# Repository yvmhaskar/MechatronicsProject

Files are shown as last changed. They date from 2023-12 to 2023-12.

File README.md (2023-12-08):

# MechatronicsProject
Project Description: Hip Exoskeleton Final Project for Introduction to Mechatronics
https://github.com/yvmhaskar/MechatronicsProject
This project can be implemented on a hip exoskeleton to conduct state estimation and positional control.
This project takes in sensor values and calculates the hip angular displacement, velocity and checks for heel strikes.
Based on the hip joint angles in each stride, the machine will change states between Level Walking, Incline and Decline.
It will also provide positional control to a thigh strut using the hip joint angles.

    Sensors: Gyroscope PMOD - Placed directly on the leg using a Sensor Mount
                            - Used to obtain gyroscope data which is used to calculate hip angular displacement and velocity
                            
             Accelerometer PMOD - Placed on the strut mounted on the motor
                                - Used to obtain accelerometer data which is used to calculate IMU spikes in the vertical direction
                                
    Actors: Pololu S03TXF STD Servo Motor - Attached to the hip actuator mount with a Motor Mount, has a thigh strut attached to it
                                          - Positional control is used to keep the thigh strut aligned with the leg
                                          
            LEDs - Attached on the breadboard on top of the myRio controller
                 - Displays the current state (Level-walking, Incline, Decline)

File Descriptions:

    Filename: Final_Project_HipExo.lvproj
        This should be used to begin/open the Final Project

    Filename: HipExo.vi
        This is the main file containing majority of the code and coordination required to conduct state estimation and positional control.

    Filename: GYRO_Read_Plot.vi
        This SubVI configures the Gyroscope PMOD, reads and plots the output data.

    Filename: Interrupts.vi
        This SubVI looks out for any interrupts inputted by the various Pmods.

    Filename: ACL_Read_Plot.vi
        This SubVI configures the Accelerometer PMOD, reads and plots the output data.

    Filename: state_typedef.ctl
        This is the type def variable used to control the changing states

CAD Descriptions:

    Filename: pololumotormount.SLDPRT
        This part is used to mount the motor to the Actuator Mount

    Filename: ActuatorMount_SweepBased_YM_v3.SLDPRT
        This part curves around the waist and holds the actuator

    Filename: LowerBackInterface_withCurvature_MW.SLDPRT
        This part connects the Actuator Mount on each side
        
    Filename: thighstrut.SLDPRT
        This part is mounted on the actuator and also holds the accelerometer

    Filename: IMU with curved handles.SLDPRT
        This part is mounted on the leg with a velcro-strap and holds the GYRO PMOD

Requirements:

| Category | No. | Threshold/Objective | Requirement | Value | Unit |
| --- | --- | --- | --- | --- | --- |
| Output | 1 | T | Motor outputs positions commanded by MyRio | T/F | |
| Output | 2 | T | LEDs indicate when the ambulation mode is changed | T/F | |
| Data Capturing | 3 | T | System will read Accelerometer values every 5ms | 5 | ms |
| Data Capturing | 4 | T | System will read Gyroscope values every 5ms | 5 | ms |
| Control | 5 | T | System can classify different modes of ambulation | 3 | modes |
| Control | 6 | O | System outputs position based on the classified ambulation mode | T/F | |
| Weight/Dimensions | 7 | T | Prototype Weight (+/-) | 3 | Kgs |
| Power | 9 | T | Prototype shall operate for 30 minutes without the need to change batteries | 30 | minutes |
| Power | 10 | O | Prototype shall operate for 2 hours without the need to change batteries | 2 | hours |

We chose the following requirements to acheive our goal of creating an hip exoskeleton which conducts
state estimation and positional control. For this we needed the motor to change positions based on the commands
and the LEDs to change colors when the ambulation mode was changed. Secondly, we needed both our sensors to
read values atleat every 5 ms to reduce the delay in movement. The exoskeleton should also be able to classify
a altitude increasing and decreasing motion along with a maintaining altitude. Therefore we set the threshold as
3 states (Level walking, Incline and Decline). We needed the system to output appropriate position based on the states
to ensure that the thigh strut can successfully follow the leg. Lastly, we wanted to have a prototype weight which is 
lower than 3 Kgs and run for atleast 30 minutes as any higher weight or lower battery time would cause a hinderance to
the wearer.

The designs for the various parts used for this project are saved as .SLDPRT files in the CAD folder of the Github Repository.
The video demonstrations for this project are placed in the Media Folder of the Github Repository.

Challenges Encountered:

- Configuring the motor to reduce the delay and provide positional control.
- The Accelerometer gets thrown off by the other foot's heel strikes.
- The joint angle values are derived from the gyroscope values and thrus slowly accumulate error.
- The motor is too weak to provide meaningful support to a human leg

Conclusion and next steps:

Our completed project met all the requirements described in our table. We are able to reliably estimate state based
on the collected sensor data and provide positional control to our actuators.

Next steps should include using a motor with a motor encoder instead of relying on a Gyroscope PMOD. Secondly
the motor can provide torque control support instead of positional control. A battery can also be used to power
the myRio controller and the motor.

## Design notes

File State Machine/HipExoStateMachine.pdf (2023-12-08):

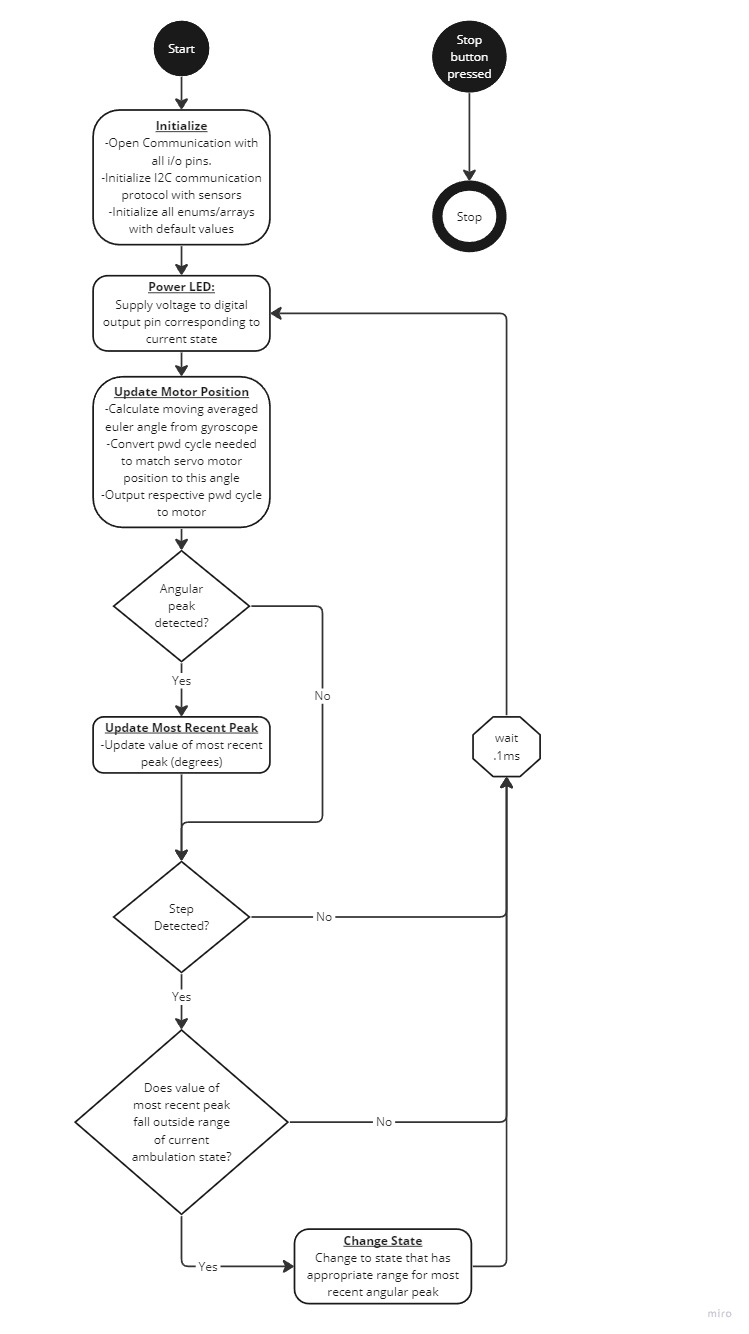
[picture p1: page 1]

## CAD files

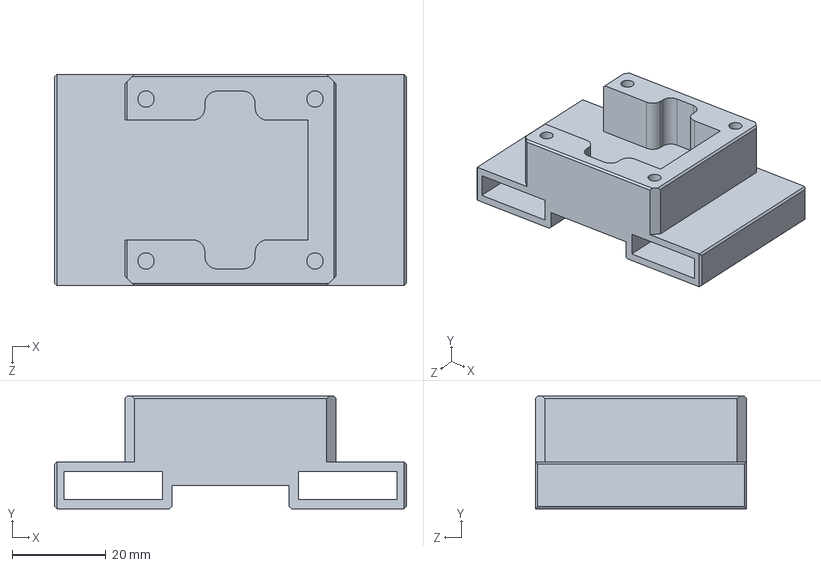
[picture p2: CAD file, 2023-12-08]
CAD/IMU holder v1.SLDPRT
75.0 x 24.0 x 45.0 mm

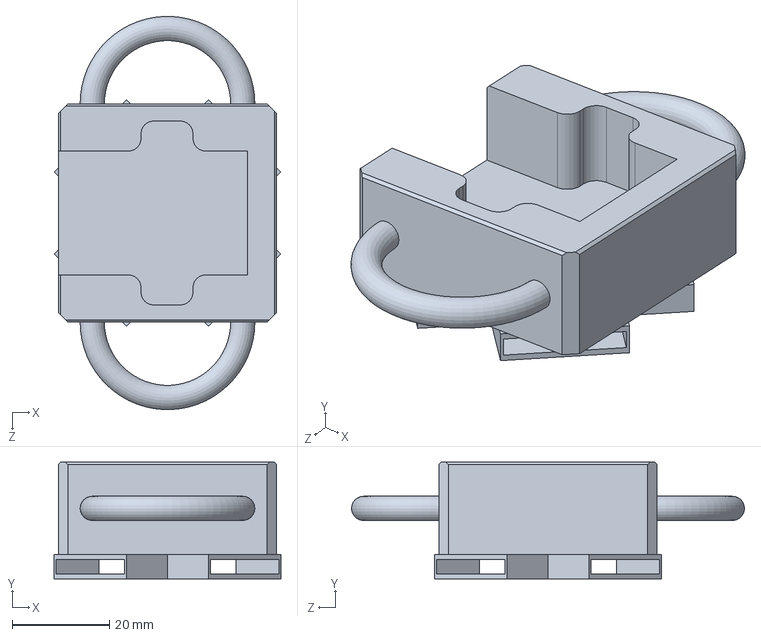
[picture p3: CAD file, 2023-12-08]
CAD/IMU with curved handles and cross straps.SLDPRT
46.7 x 24.0 x 81.0 mm

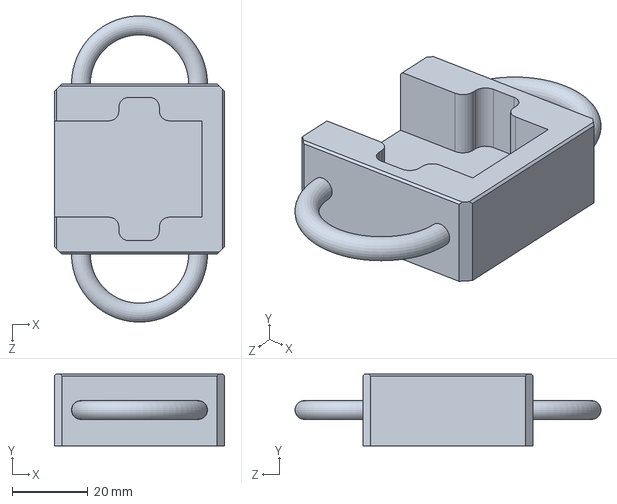
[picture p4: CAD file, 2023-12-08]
CAD/IMU with curved handles.SLDPRT
45.0 x 19.0 x 81.0 mm

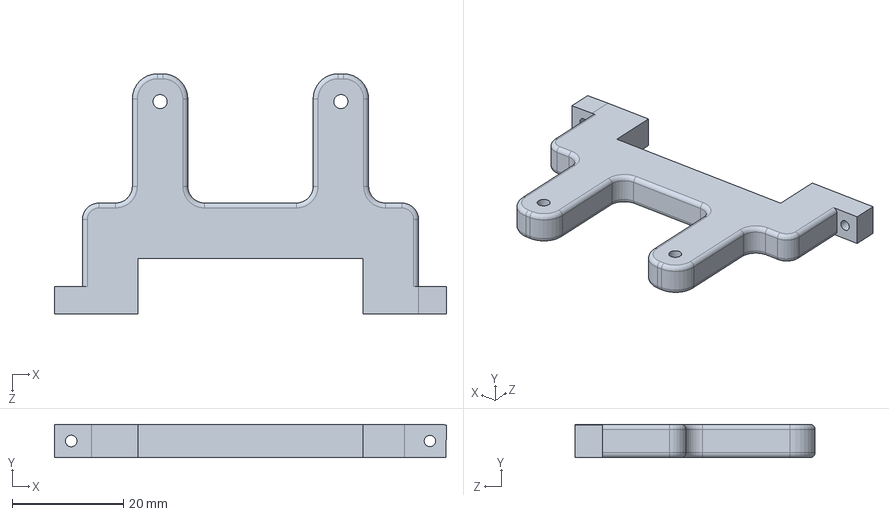
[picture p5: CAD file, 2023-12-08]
CAD/pololumotormount.SLDPRT
70.5 x 6.00 x 43.2 mm

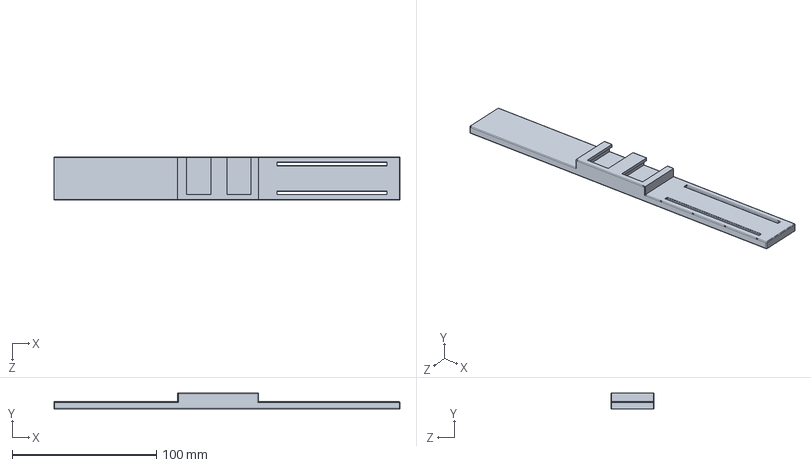
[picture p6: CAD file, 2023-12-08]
CAD/thighstrut.SLDPRT
240.0 x 11.0 x 30.0 mm

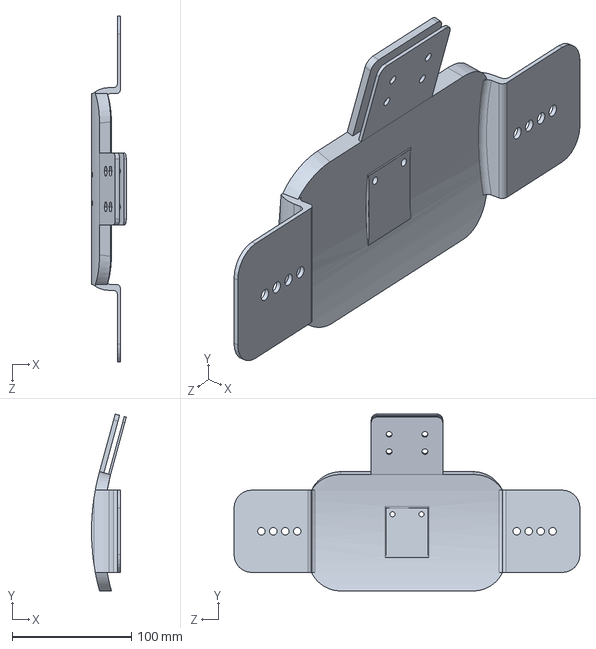
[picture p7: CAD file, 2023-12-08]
CAD/LowerBackInterface_withCurvature_MW.SLDPRT
29.0 x 148.2 x 290.0 mm

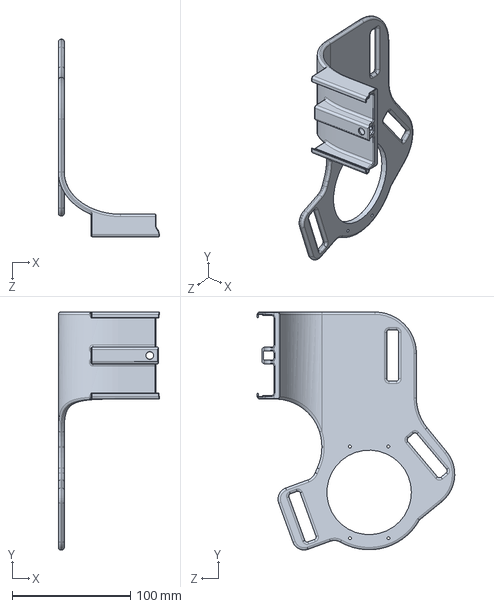
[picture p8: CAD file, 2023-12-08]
CAD/ActuatorMount_SweepBased_YM_v3.SLDPRT
85.5 x 201.1 x 166.9 mm
